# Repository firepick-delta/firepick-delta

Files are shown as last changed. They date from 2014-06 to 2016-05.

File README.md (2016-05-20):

### FirePick Delta Hardware/Mechanical Repo

#### Summary / Context

Design and Manufacturing Specifications for [FirePick Delta](http://delta.firepick.org).  If you're a developer wanting to help, the best way to do that is to join the [mailing list](https://groups.google.com/forum/#!forum/firepick) and start a line of communication there.  

This repo only contains the hardware (sch/pcb) and mechanical (3d) files for FirePick Delta.  It inherits software from OpenPnP, Marlin, and FirePick.  Other repo's of interest for FirePick Delta:

* https://github.com/firepick-delta/openpnp
* https://github.com/firepick-delta/Marlin
* https://github.com/firepick1/FireREST
* https://github.com/firepick1/FireBOM

#### Mechanical Assembly Parts Tree, Instructions, and BOM

Please click the link below to navigate the mechanical assembly with our FireBOM wiki documentation system:

[AFPD0001](AFPD0001) FirePick Delta Hacker-Developer Edition

#### Licensing

CC-BY-SA

These files are licensed under [*Creative Commons Attribution-ShareAlike (CC BY-SA)*](https://creativecommons.org/licenses/by-sa/4.0/legalcode).  Commercial use is OK, but you are required under the license conditions to share your changes with the internet, and also credit the FirePick Delta team.

This license lets others remix, tweak, and build upon your work even for commercial purposes, as long as they credit you and license their new creations under the identical terms. This license is often compared to “copyleft” free and open source software licenses. All new works based on yours will carry the same license, so any derivatives will also allow commercial use. This is the license used by Wikipedia, and is recommended for materials that would benefit from incorporating content from Wikipedia and similarly licensed projects. 

[View License Deed](http://creativecommons.org/licenses/by-sa/4.0/) | [View Legal Code](https://creativecommons.org/licenses/by-sa/4.0/legalcode)

#### Contributors
* [@FlyingLotus1983 (Neil Jansen)](https://github.com/FlyingLotus1983)
* [@firepick1 (Karl Lew)](https://github.com/firepick1)
* [@ChristianLerche (Christian Lerche)](https://github.com/ChristianLerche)
* [@daytonpid (Dayton Pidhirney)](https://github.com/daytonpid)
* [@codedetail (Dave Shanklin)](https://github.com/codedetail)
* [@obnauticus (Thomas Kilbride)](https://github.com/obnauticus)
* [@mstegen (Mike Stegen)](https://github.com/mstegen)
* [@mikeanton (Mike Anton)](https://github.com/mikeanton)

#### Maintainers
* [@FlyingLotus1983 (Neil Jansen)](https://github.com/FlyingLotus1983)
* [@firepick1 (Karl Lew)](https://github.com/firepick1)

#### Contributions and Pull Requests

If you'd like to contribute anything back to this repo, please do so via [pull requests](https://help.github.com/articles/using-pull-requests).  

Keep in mind that the Cubify Design files are binary blobs.  Assembly (AD_ASM) files contain filepath links back to dependent solid parts (AD_PRT), and parts contain filepath links back to the assembly.  This makes it extremely tricky to use version control.  You can't just rename files all willy-nilly, or else Cubify will get very angry.  Please excercise caution and contact the FirePick Delta Dev Team via [google group mailing list](https://groups.google.com/forum/#!forum/firepick) before attempting to modify anything of significant nature.

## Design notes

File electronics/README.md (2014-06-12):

### Electronic Design Directory

To add a new circuit design, first choose a new ID:

* **E** is the ID prefix for electronic parts (e.g., [ECAM01](../../../wiki/ECAM01)).

Archive your new design in git:

1. `git checkout dev`
1. Create a new directory (e.g., **ecam01**) and add your design files
1. `git add --all`
1. `git commit -am "adding new PCB"`
1. `git fetch; git merge; git push`

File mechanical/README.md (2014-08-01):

### 3-D Mechanical Design Directory

#### Summary / Context

This directory contains the mechanical files for  [FirePick Delta](http://delta.firepick.org).  If you're a developer wanting to help, the best way to do that is to join the [mailing list](https://groups.google.com/forum/#!forum/firepick) and start a line of communication there.  

#### Licensing

CC-BY-SA

These files are licensed under [*Creative Commons Attribution-ShareAlike (CC BY-SA)*](https://creativecommons.org/licenses/by-sa/4.0/legalcode).  Commercial use is OK, but you are required under the license conditions to share your changes with the internet, and also credit the FirePick Delta team.

This license lets others remix, tweak, and build upon your work even for commercial purposes, as long as they credit you and license their new creations under the identical terms. This license is often compared to “copyleft” free and open source software licenses. All new works based on yours will carry the same license, so any derivatives will also allow commercial use. This is the license used by Wikipedia, and is recommended for materials that would benefit from incorporating content from Wikipedia and similarly licensed projects. 

[View License Deed](http://creativecommons.org/licenses/by-sa/4.0/) | [View Legal Code](https://creativecommons.org/licenses/by-sa/4.0/legalcode)

#### File Format
These files were created in [Cubify Design](http://cubify.com/Products/Design).  Cubify Design is admittedly not an open-source program, and costs $199 to buy, with a 30-day free trial.  It gives about 50% of the functinoality of SolidWorks, for a fraction fo the price.

We would have loved to use an open-source program for FirePick Delta, but none of them were up to the job.  OpenSCAD, for example, still doesn't (easily) support fillets or other simple primatives.  HOWEVER, we are making the STL versions of these files available now, and will be offering converted versions of all of the mechanical files in this repo in other, more common 3d formats, in the near future, including STEP, IGES, SCAD, and others.  The basic idea is to design in Cubify and, when the files have stabilized, re-draw in industry-standard formats.  

If you're decent with mechanical design software, and would like to volunteer to help us with this effort, please get in touch with us at our [google group malining list](https://groups.google.com/forum/#!forum/firepick).

#### Contributions and Pull Requests

If you'd like to contribute anything back to this repo, please do so via [pull requests](https://help.github.com/articles/using-pull-requests).  

Keep in mind that the Cubify Design files are binary blobs.  Assembly (AD_ASM) files contain filepath links back to dependent solid parts (AD_PRT), and parts contain filepath links back to the assembly.  This makes it extremely tricky to use version control.  You can't just rename files all willy-nilly, or else Cubify will get very angry.  Please excercise caution and contact the FirePick Delta Dev Team via [google group mailing list](https://groups.google.com/forum/#!forum/firepick) before attempting to modify anything of significant nature.

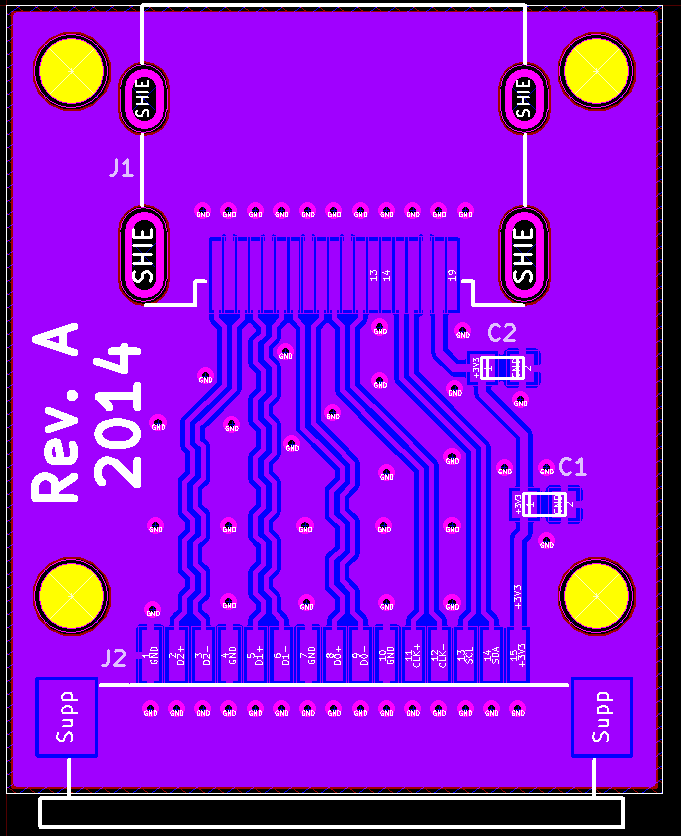
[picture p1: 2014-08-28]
electronics/ehdmifpc01/HDMI to FPC PCB.png

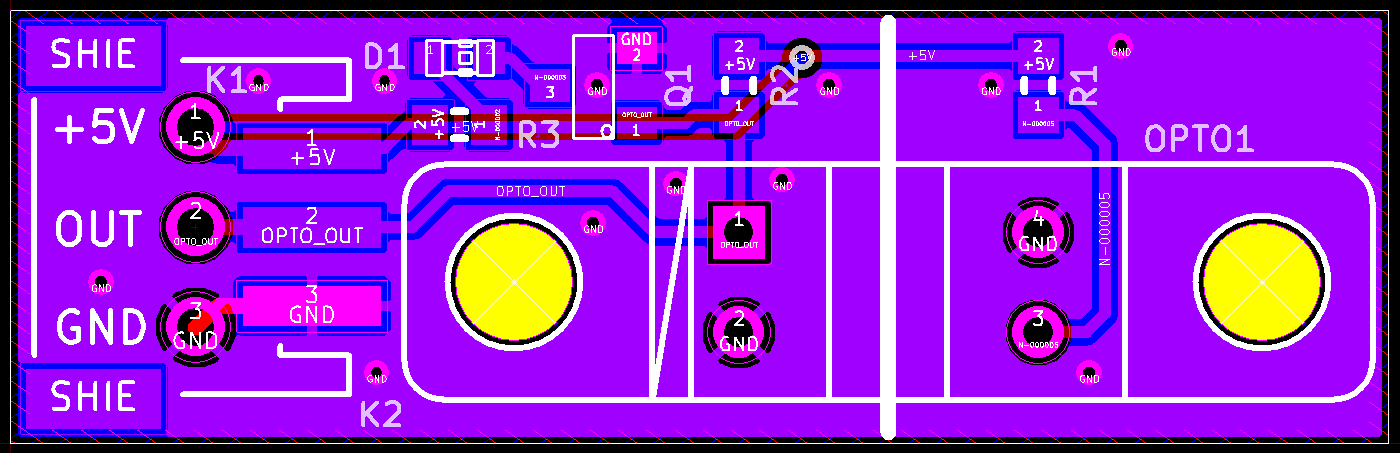
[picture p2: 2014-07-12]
electronics/eopto01/KiCAD/eopto01.png

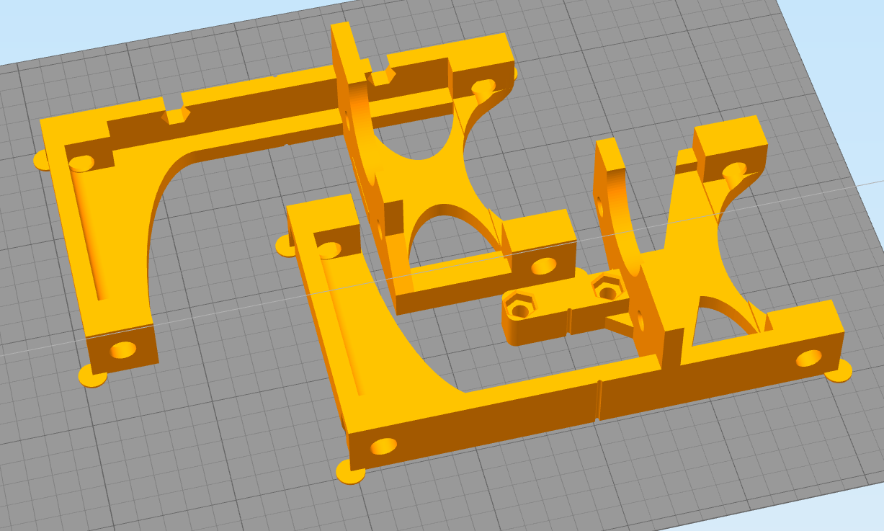
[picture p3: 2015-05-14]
Documentation/STL images/3D0456 Delta stepper mount.png

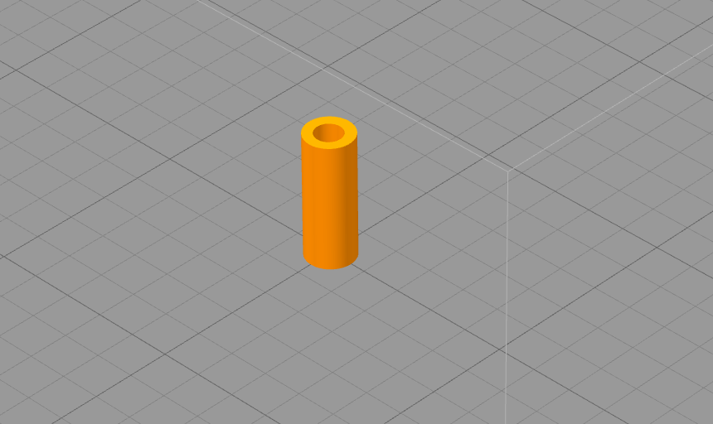
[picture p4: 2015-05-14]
Documentation/STL images/FSTN-M3-18L-UNTHREADED.png

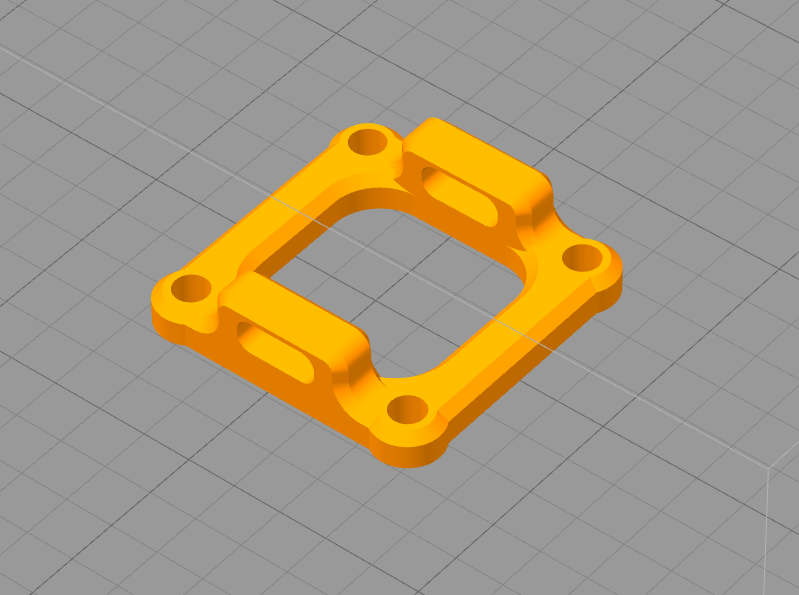
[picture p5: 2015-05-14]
Documentation/STL images/3DAT0015c - Camera-to-end-effector mount - downward endocam.png

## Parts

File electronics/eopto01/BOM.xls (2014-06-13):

Part | Quantity | Price (USD) | Total
--------------------------------------------------------------------------------------------
TCST2103 | 1 | 2.18 | 2.18
Red 0805 LED | 1 | 0.04 | 0.4
10K Resistor 0805 | 1 | 0.04 | 0.04
150 Ohm Resistor 0805 | 1 | 0.04 | 0.04
68 Ohm Resistor 0805 | 1 | 0.04 | 0.04
3 Pin Header “0.1 Spacing | 1 | 0.1 | 0.1
 |  |  | 2.8

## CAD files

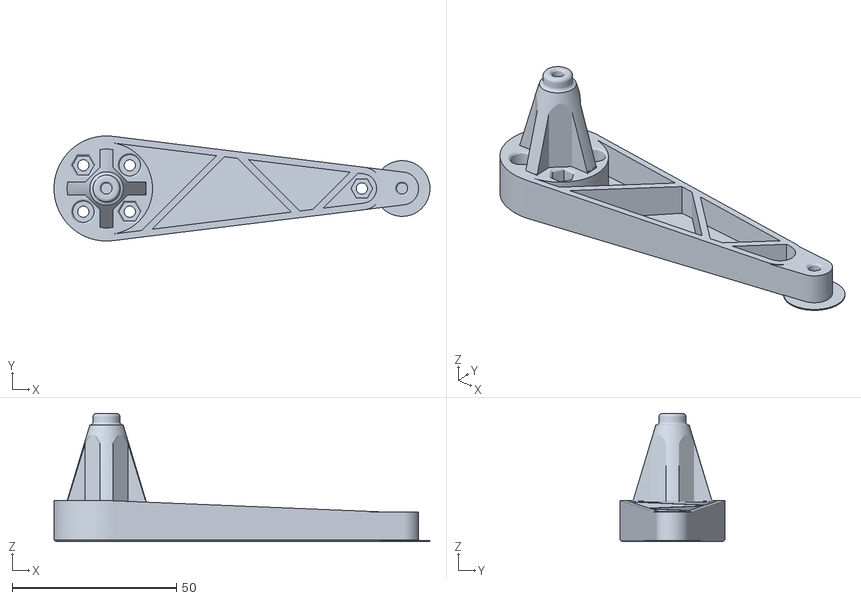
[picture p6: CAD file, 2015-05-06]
Production Files/3D printed pieces - STL - Orange/3D0003a - Delta motor assembly - Delta arm 90mm.stl
114.5 x 32.0 x 39.0

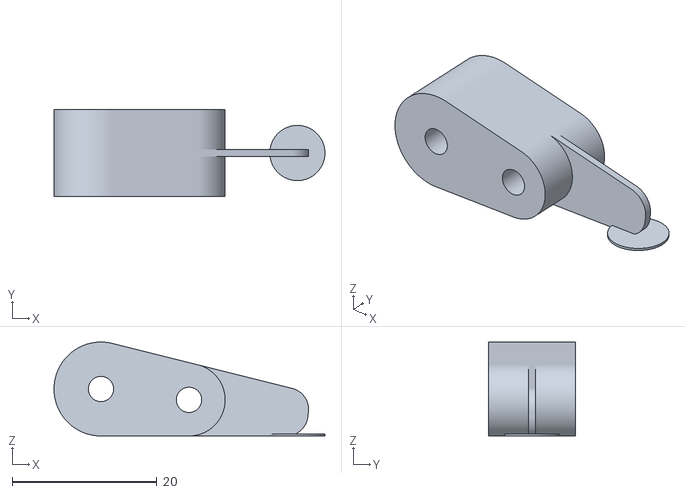
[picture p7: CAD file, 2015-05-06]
Production Files/3D printed pieces - STL - Black/3D0007 - Delta motor assembly - Limit switch interruptor.stl
37.5 x 12.0 x 13.0

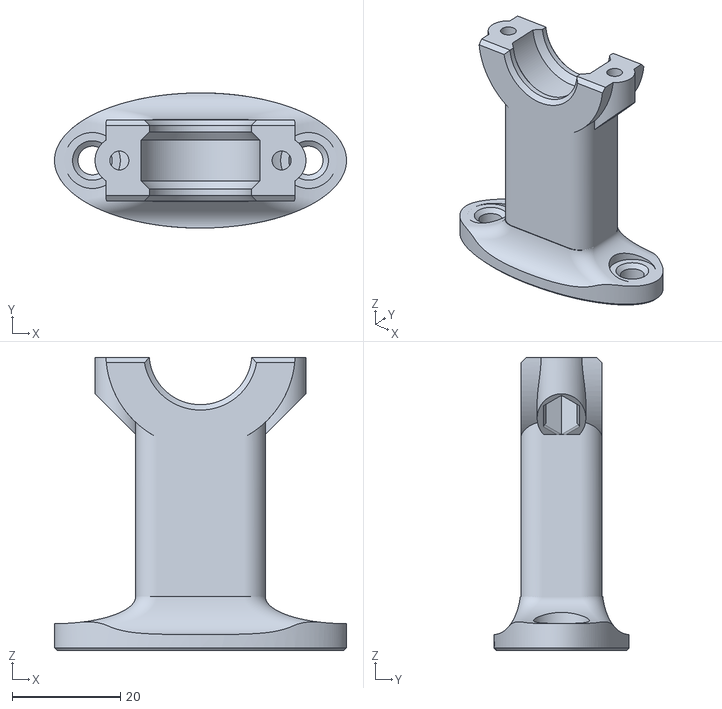
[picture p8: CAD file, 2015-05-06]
Production Files/3D printed pieces - STL - Black/3D0001a - Delta motor Assembly - 608 bearing block.stl
54.0 x 25.0 x 54.3

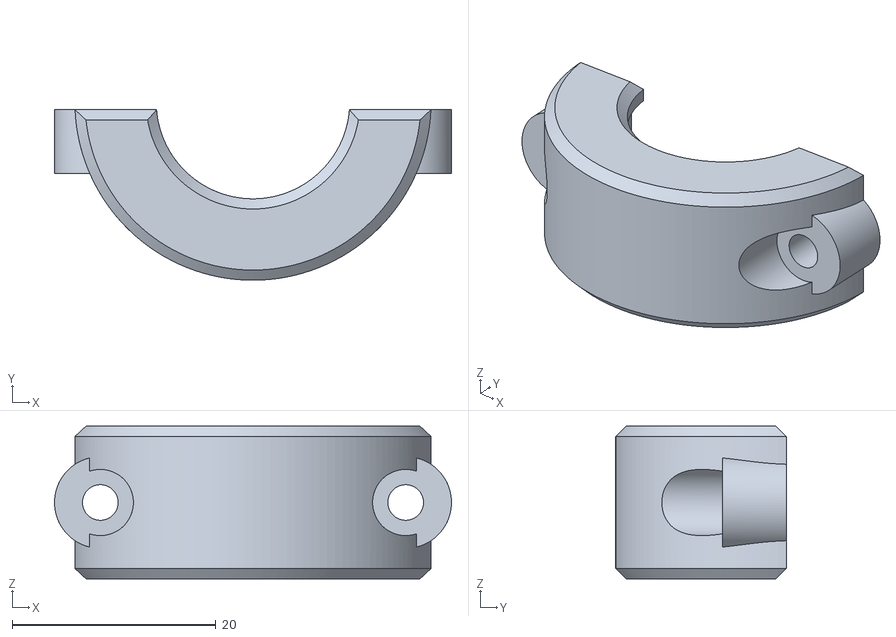
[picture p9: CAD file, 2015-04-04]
Production Files/3D printed pieces - STL - Black/3D0004 - Delta motor Assembly - 608 bearing block caps.stl
39.0 x 16.8 x 15.0

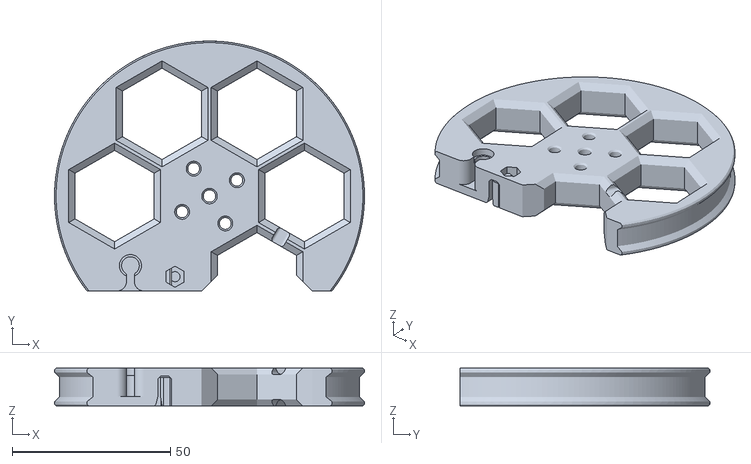
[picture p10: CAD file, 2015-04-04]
Production Files/3D printed pieces - STL - Black/3D0002b - Delta motor assembly - Pulley (150T).stl
98.0 x 79.0 x 12.0

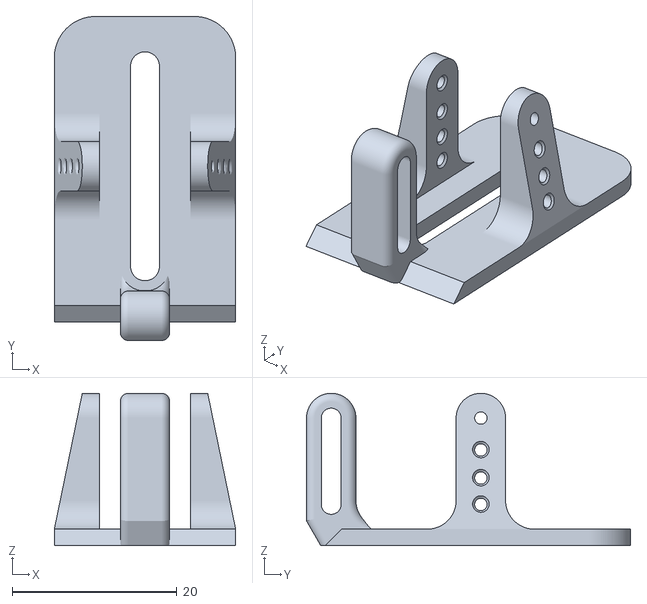
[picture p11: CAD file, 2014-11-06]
mechanical/Hxxx - Hacks/STL/H0003 - Hinged Camera Slide.stl
22.0 x 39.3 x 18.5

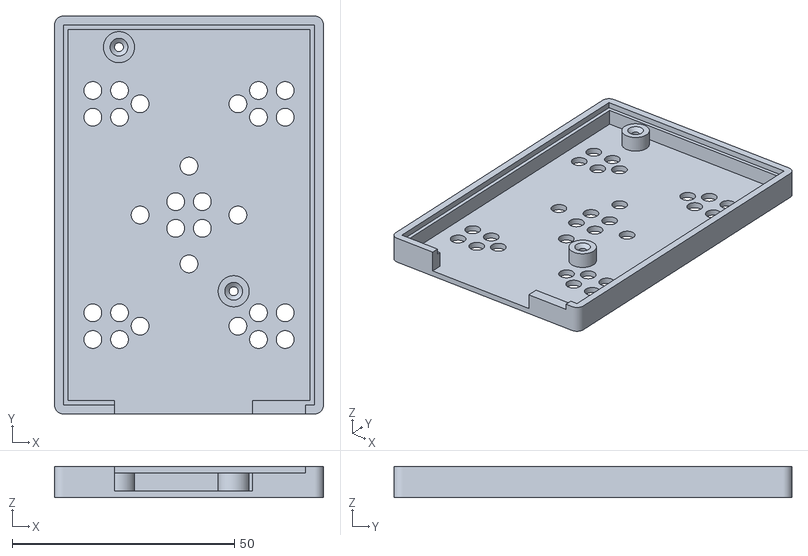
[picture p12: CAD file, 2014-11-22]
mechanical/Jxxx - Jigs and test fixtures/STL/J0013 - RasPi B base.stl
60.5 x 89.5 x 7.00

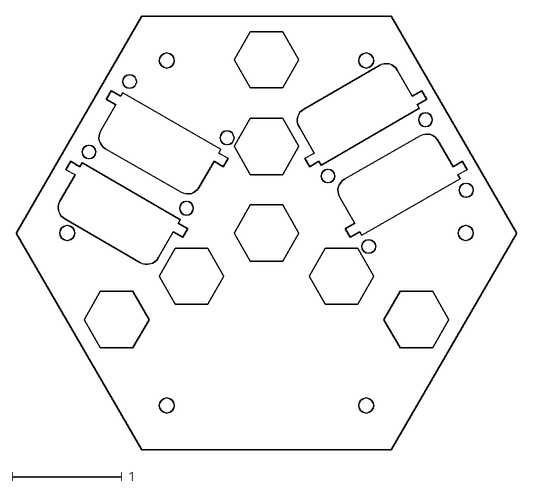
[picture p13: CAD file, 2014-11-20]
mechanical/Pxxx - Panels/DXF/PC04.dxf
4.55 x 3.94

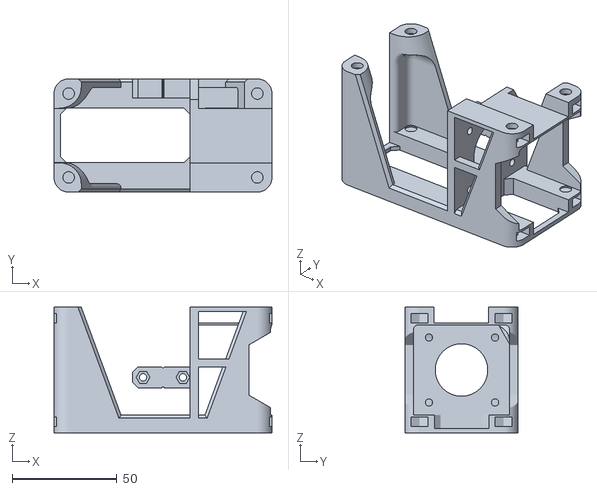
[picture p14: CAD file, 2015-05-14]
Production Files/3D printed pieces - STL - Black/3D0456c Delta stepper mount.stl
104.0 x 54.0 x 60.0

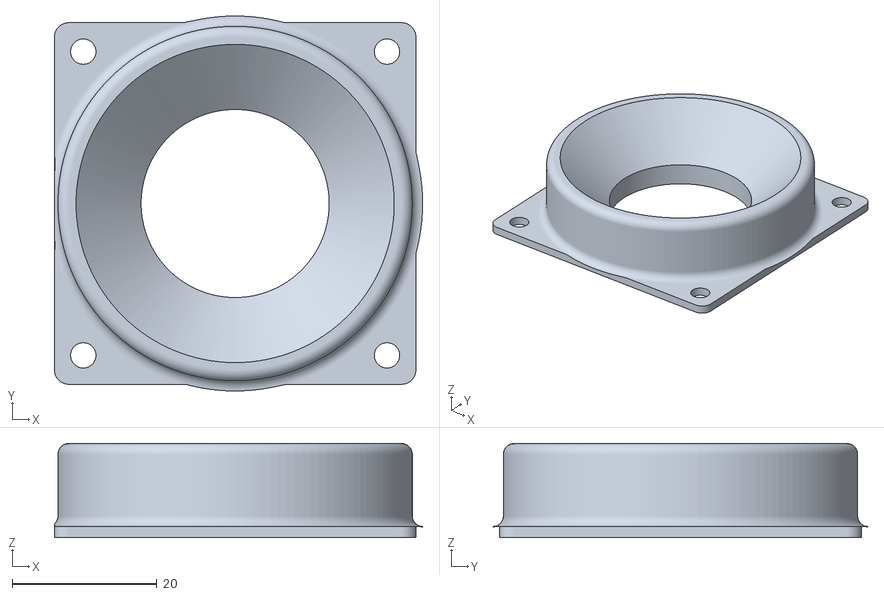
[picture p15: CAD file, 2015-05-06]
Production Files/3D printed pieces - STL - Clear/3D0030b - Up-looking camera housing diffuser - ELP-USB100W03M.stl
50.9 x 51.9 x 13.0

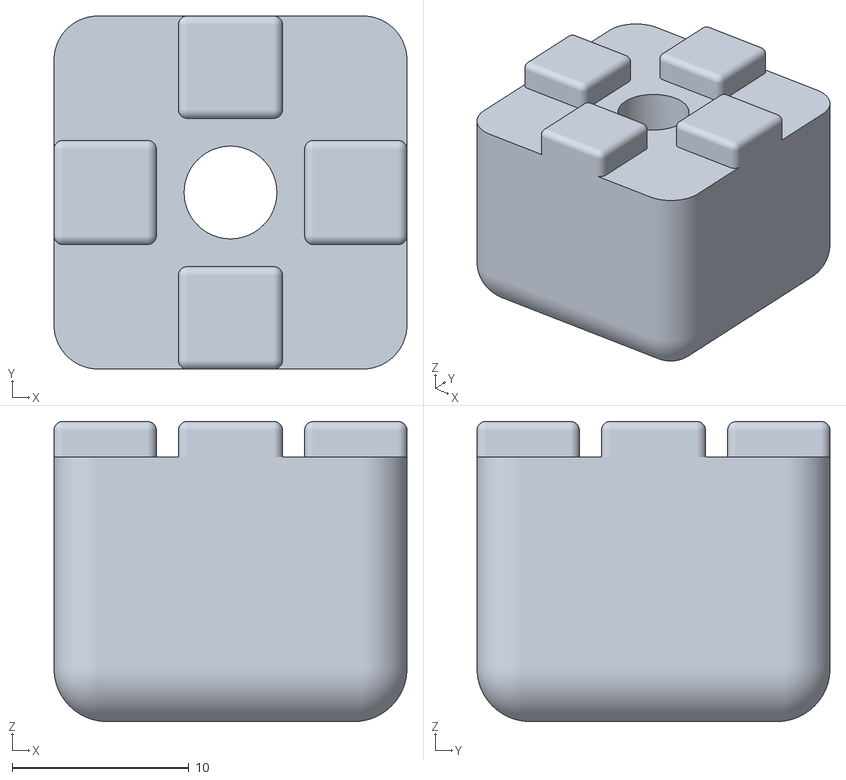
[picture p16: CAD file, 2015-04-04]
Production Files/3D printed pieces - STL - Flexy/3D0025 - Rubber Foot.stl
20.0 x 20.0 x 17.0

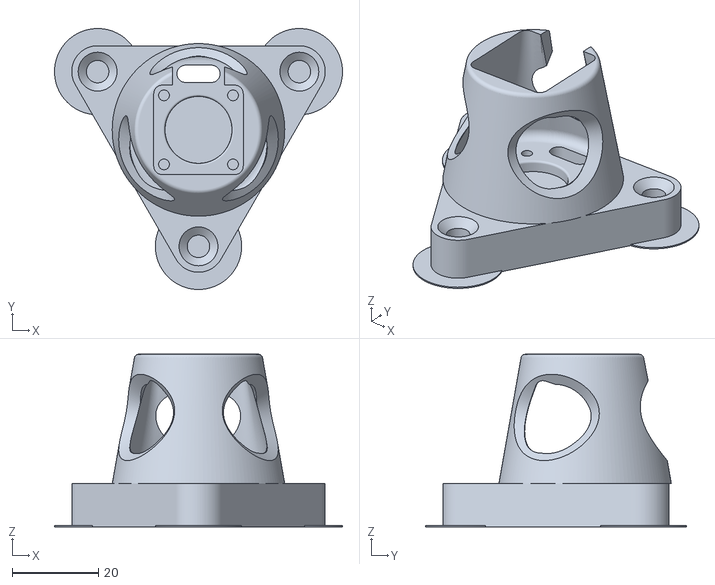
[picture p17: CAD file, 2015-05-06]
Production Files/3D printed pieces - STL - Orange/3DAT0021a - NEMA8 mount.stl
66.8 x 60.5 x 40.0

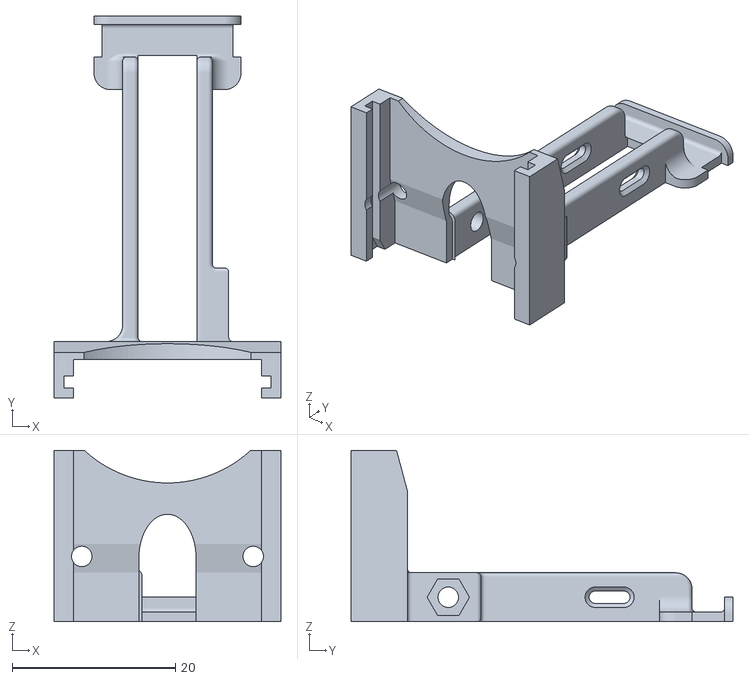
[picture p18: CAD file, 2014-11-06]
mechanical/Hxxx - Hacks/STL/H0002 - RPiCam Hinged Camera Mount.stl
27.8 x 46.7 x 21.0

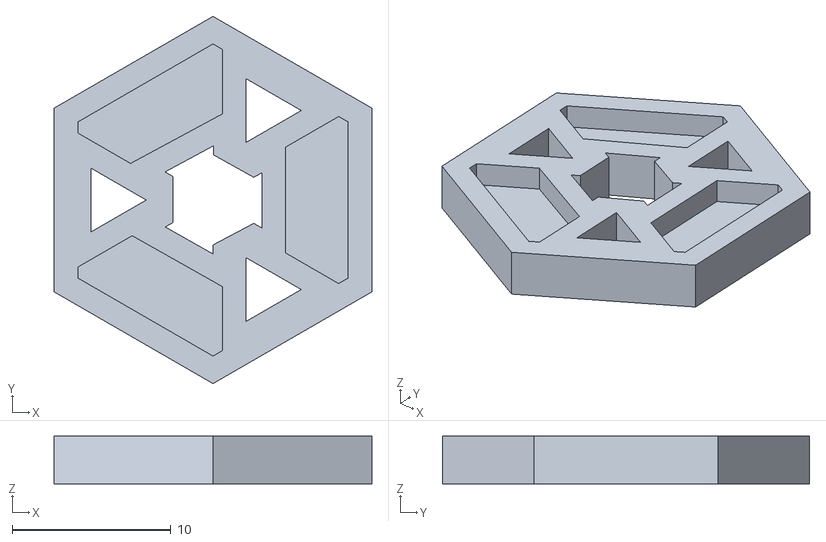
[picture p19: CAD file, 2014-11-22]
mechanical/Jxxx - Jigs and test fixtures/STL/J0001A - Raspberry Pi camera wrench.stl
20.0 x 23.1 x 3.00

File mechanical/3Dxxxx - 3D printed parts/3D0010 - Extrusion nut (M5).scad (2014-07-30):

module box(w,h,d) {
	scale ([w,h,d]) cube(1, true);
}
module hexagon(height, depth) {
	boxWidth=height/1.75;
		union(){
			box(boxWidth, height, depth);
			rotate([0,0,60]) box(boxWidth, height, depth);
			rotate([0,0,-60]) box(boxWidth, height, depth);
		}
}

module nut() {
rotate([180,0,0]) difference() {
	translate([-6, -7.5, 0]) rotate([270,0,0]) linear_extrude(height=15) polygon([ [0,0], [12, 0], [12, 1], [9.2, 3.8], [2.8, 3.8], [0, 1] ]);
	translate([0,0,-1.2]) cylinder(r=5, h=1.2, $fn=100);
	translate([0,0,-4]) rotate([0,0,90]) hexagon(8, 8);
}
}

for(x=[0:6]) for(y=[0:5]) {
	translate([x*13, y*16, 0]) nut();
}

*translate([-6, -7.5, 0]) cube([120, 120, 1]);

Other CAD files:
mechanical/Pxxx - Panels/DXF/PC01 - Top plate.dxf
Production Files/3D printed pieces - STL - Black/3DAT0012a - 3D printer mount_NoSupport.stl
Production Files/3D printed pieces - STL - Clear/3DAT0010a - End effector - ATC hub (bottom).stl
Production Files/3D printed pieces - STL - Orange/3D0053 - External ATX supply coverplate.stl
Production Files/3D printed pieces - STL - Black/3D0010a - Extrusion nut (M3).stl
Production Files/3D printed pieces - STL - Black/3D0015a - EMC02 mounting plate.stl
Production Files/3D printed pieces - STL - Black/3D0021 - EMC01 Modular tool card-cage.stl
Production Files/3D printed pieces - STL - Black/3D0026b - Up-looking camera housing base - ELP-USB100W03M.stl
Production Files/3D printed pieces - STL - Black/3D0028 - PCB magnet holder.stl
Production Files/3D printed pieces - STL - Black/3D0456 Delta stepper mount (unibody).stl
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

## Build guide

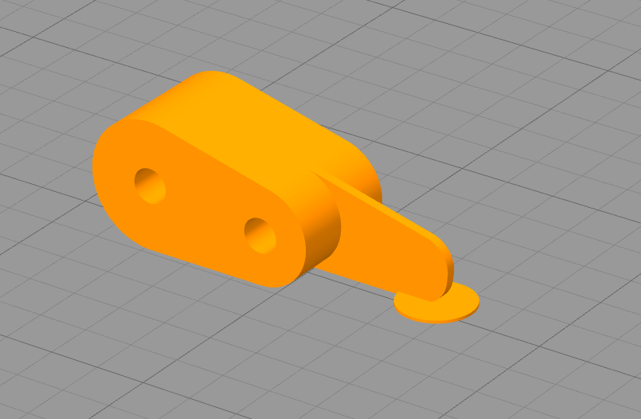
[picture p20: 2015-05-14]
Documentation/STL images/3D0007 - Delta motor assembly - Limit switch interruptor.png

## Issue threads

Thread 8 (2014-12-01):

3D0230a and clearence issues

PeeJay, 2014-12-01:
Hi Neal/Karl
I have just been assembling my arms (the ball end type) and I've had some trouble getting them to fit.
1) The spring (3D0230a) has 2mm holes when both spring socket holders have 3mm - I pressume this is just an oversight, as it all lined up when I printed another set of springs with 3mm holes.
2) When I printed the spring socket holders there was some very slight curling along the edges, but the clearance between the spring and spring socket holders is so small that the upper spring socket holder is binding on the spring. If you look at the lower spring socket holder there is a slit that prevents this binding, so I would suggest to create something similar on the upper spring socket holder.

FlyingLotus1983, 2015-05-30:
Closing issue.  We're not using catenary springs in this repo any more (catenary springs can be found over in Karl's repo, at https://github.com/firepick1/FPD-LooseCanon )

firepick1, 2015-05-30:
For those of you with LooseCanon parts, I apologize for the collision. My interim solution is to use the LooseCanon optical switch interruptor, which has a rake-back angle that prevents the collision. I'll eventually address this, but am currently busy with calibration and motion as a priority.

Closed 2015-05-30.

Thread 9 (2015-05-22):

Outline is in the silkscreen layer, not the dimension issue

FlyingLotus1983, 2015-05-22:
Look through all of the production boards, just to be sure.

bgbock, 2015-05-23:
EPWR01 board

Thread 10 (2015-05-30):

LED ring lights may be too dim -- need weigh-in from the beta test kit owners

FlyingLotus1983, 2015-05-30:

cdsteinkuehler, 2015-05-30:
I think you've got the specs backwards, the white LED has a 3.2V (typ) forward voltage and the red LED has 1.8V.  Given there are two LEDs in series, it seems amazing if the white LED board lights at all (given a combined typical forward voltage of 6.4V)!  The values for the red LED board seem a bit small if you want 10 mA (the value given yields a typical forward current around 13 mA, 150 ohm should yield a bit under 10mA at 5V).  If you want to run the white LEDs off of 5V, they need to each have their own current limiting resistor of around 100 ohms (for 20 mA forward current)...or the existing 120 ohm parts would work well if there weren't two white LEDs in series.

For a short-term fix, I suspect if you simply short across every-other white LED, you'll get much more light output than with the existing circuit.  This should be easy to test, but I don't have the parts to build an LED board, and I didn't get an assembled one in the bare-bones kit.

FlyingLotus1983, 2015-05-30:
Thanks Charles, you're right, I've corrected my initial post with the correct voltages.

If you'd be interested, I could supply you with the red / white LEDs and the 2x BSS138's if you'd be willing to help us with this issue.  I'll mail you the parts free of charge (we have enough of them on a reel, lol).  As for resistors, I recommend this guy: https://www.adafruit.com/products/441 Great tool for any hardware guy's arsenal.

cdsteinkuehler, 2015-05-30:
Send me the LEDs and FETs, the resistor's I've already got on-hand
(all 5% and 1% values between 1R and 10M in 0603 and 0805).  Sometimes
it's handy to design electronics for a living!  :)

IMHO, the LEDs probably ought to be run off 12V if possible,
particularly the white ones.  It's hard to drive that many white LEDs
with only 5V w/o wasting a lot of power (unless you're using "smart"
switching drive circuits to regulate the current instead of plain old
resistors).  Quick back-of-envelope calculation shows if you assume 20
mA LED drive, you're burning 1W in the LEDs, and 600 mW in the
resistors at 5V, or enough you probably need to think about things
getting warm.

--
Charles Steinkuehler
charles@steinkuehler.net

FlyingLotus1983, 2015-05-30:
We're using an ATX power supply for the resistors, sourcing current on the
5V rail won't be a problem.  Putting it on 5V makes the wiring a lot
easier, but I agree that it isn't ideal to drive LEDs with it.

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

--
Neil Jansen, Co-Founder
Tin Whiskers Technology, LLC
http://tinwhiskers.io

rotorfixer, 2015-05-30:
Yes, I have to agree, the source voltage is too low for two of those in series.

Can you post the part numbers of the capacitor and mosfet as well so I can look at supplying the board with 12VDC?

I will also try out Charles' suggestion of using a 0 ohm resistor over one of the LEDs and see what the light output is with half the LEDs, but powered properly.

Peter.

FlyingLotus1983, 2015-05-31:
MOSFET is a standard BSS138 (We used a Fairchild part, digikey P/N is BSS138CT-ND).

Capacitor is a pretty standard electrolytic 16V, 6.3mm diameter, around 100 uF.

Powering the boards with 12V is possible, but the wiring gets a little uglier.

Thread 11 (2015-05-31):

Vacuum pump mount screw is too long

shmuelzon, 2015-05-31:
The vacuum pump mount comes with a 14mm screw in order to mount it to the frame, however I found that this screw is too long and won't hold the mount firmly to the frame. The 10mm ones work great.

FlyingLotus1983, 2015-05-31:
Yikes, I can't believe I missed that.  I'm fixing it on the 3D model now.  Will try and get the BOM and packing list updated as well.

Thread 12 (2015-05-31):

Fan mounting screws are too short

shmuelzon, 2015-05-31:
The screws provided for mounting the fan are too short. It seems that the fan I got is thicker than what was expected (at least it seems higher relative to the drawing)

FlyingLotus1983, 2015-05-31:
This was a screw-up by our Chinese supplier.  We didn't get the fans that we were supposed to. They listed them as 10mm thick and we got these giant monstrosities.  We didn't measure them until after we got a few complaints.

I'm unsure if I should update my model, as it's probably the last time I'm buying from this supplier again, meaning that the BOM and model are actually correct and the fans that are incorrect.  But for the beta kit customers, I will need to send them updates screws for the bigger fans.

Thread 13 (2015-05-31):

No room to mount EAT0002

shmuelzon, 2015-05-31:
There is not enough room to mount the EAT0002 board at slot 1 after I connected the EAT0004 board at slot 2. Perhaps if I remove the heatsink it will fit. I connected the module cards as described in the [documentaiton](http://delta.firepick.org/documentation). See [photo](https://plus.google.com/photos/+AssafInbal/albums/6153966946821929473/6154602321539083746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).

FlyingLotus1983, 2015-05-31:
This is a confirmed issue, I've had to remove the heatsink on my two FPD machines.  The slot spacing on the EMC02 was designed for the EAT0001 style boards that had integrated DRV8825's on the board.  The EAT0002 came later as a way to mitigate some of the SMT produciton issues we were having.  But using the StepStick driver modules are admittedly bulky and cause issues.

Regretfully the short-term workaround is to just run it without the heatsink. The SMT module will be fine like this, and I haven't had issues with the Wade etruder yet.  Will be very interested to see if others have problems.  I'll leave this issue open for the entire beta run, to get more opinions and user accounts.

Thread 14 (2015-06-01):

Missing M3 screw and nut for the small gear of the extruder

shmuelzon, 2015-06-01:
It seems that the exploded view (and, as a consequence, the BOM and beta kit) of the extruder is missing an M3 screw and nut used to attach the small gear to the stepper motor

FlyingLotus1983, 2015-06-02:
This has been fixed in the model, and I will be starting the process of getting the BOM info to trickle down into the packing lists, bag labels, and drawings.  Will keep this issue open until all of that work has been completed, and everyone that ordered full beta kits receives their replacement parts.

FlyingLotus1983, 2015-06-02:
Everything should be updated now.  Some of the thumbnails of the PDF might be out of date, but the google docs PDF is what should be used for reference, and it's been updated in-place without changing the link.  The BOM has been updated as well.

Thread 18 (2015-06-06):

Hobbed bolt not center to input filament

alanNz, 2015-06-06:
For some reason it was way off on mine, I reduce the spacer 3DAT0028 by 3 - 3.5 mm to get alignment

FlyingLotus1983, 2015-06-06:
I designed the spacer specifically for the RobotDigg hobbed bolt's spacing.  On my machines here, they match up perfectly.

I would like to see some measurements from your hobbed bolt to see if it's simply manufacturing variation from the hobbing process, or if it's something else.  The measurement I'm wondering about is from the bottom of the bolt head to the center of the hobbed area.  Could you measure that?  Also, could you post pics of your setup, both assembled and un-assembled?

And is it possible that there's some support material in the bearing pocket of the extruder housing?  That would cause a mis-alignment.  That area needs to be perfectly smooth, and might take a razor blade or other tool to get it perfect.

alanNz, 2015-06-06:
the bearing in the plastic gear side sits flush, the hex head of the bolt sits flush, the pocket looked pretty clean. the Hobbed bolt measurement is 27mm to the center
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

FlyingLotus1983, 2015-06-06:
I think I see the issue now :(

Your spacer should be 8.5mm.  I'm wondering if this was a failed part that should have been thrown away.  Could you send pictures of both top and bottom side?  If this is in fact the problem, I can mail you out a replacement spacer.

The hobbed distance should be at 30mm by the way, so 27 is probably close enough.

alanNz, 2015-06-06:
I've reduced the size of that spacer until it lined up so it probably was a good print. 3mm difference in center is huge! well to me it is lol

I didn't take a before shot unfortunately, it looked like the hobbed bolt would slip/ jam on the filament as it came thru since its going across the smooth section. I've re created what the 3 mm offset looked like in the attached picture.

From a kit point of view you could pack 10 x 1mmwashers so it can be tweaked to overcome manufacturing defects.
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

FlyingLotus1983, 2015-06-06:
OK, I understand now.  I think your hobbed bolt is the problem then.  Sounds like you've made it work, so that's good.  We'll certainly try to come up with a more fool-proof way to do this in the future.  I personally measured 10-15 of them before I made that spacer.  I felt that was better than 4-7 standard M8 washers, which have a pretty significant tolerance stack-up.

alanNz, 2015-06-06:
yea washer's don't look pro either. If you made a 5.5mm plastic spacer + 2mm spacer + 1mm spacer + .5 spacer etc. or 5.5mm, 6.5mm 7.5mm, 8.5mm  etc. Or turn the hobbed bolt into a hobbed threaded rod then you have your double nut on both ends for infinite adjustment.

alanNz, 2015-06-06:
or you just add the step i did, rub spacer on sand paper until it lines up. And then get you bobbed bolt guy to get there act together and spec to +/- 0.5mm which "should" be easy on these!

FlyingLotus1983, 2015-06-06:
Right.  E3D sells a hobbed bolt with threaded ends on both sides, they did this for the same reason.. it makes it a lot more adjustable.  Sadly their price is probably 10x to 25x the price of the one we used in this kit.

alanNz, 2015-06-06:
I always liked the look of these, used in diferent extruder that I've never actually used so cant coment on how well they actually work http://www.aliexpress.com/item/J35-Free-Shipping-Extruder-MK7-Stainless-Steel-Drive-Gear-Hobbed-Gear-For-Reprap-3D-Printer/32219482655.html

FlyingLotus1983, 2015-06-06:
Several problems with those (direct drive) types.  Lower torque, and heat conducted from the stepper motor into the hobbed disc can cause the filament to go mushy.  Lots of people use them, but I've never been a fan of them. I do really like Wade extruders, but as you've seen, they can be trick to setup.  The good news is that after they're setup, they require little to no maintenance, and have proven to be very reliable.

cyberreefguru, 2015-07-30:
I had to shave my space down to ~5.8mm to get the hobbled bolt to align properly.  YMMV.

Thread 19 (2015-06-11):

Effector warping

ristola, 2015-06-11:
Finally got the 3D printer ready and have been working on configuration as it was printing 95% of full size. Was printing 10mm and 20 mm cubes. Everything was perfect.  Then things started changing. Then I started to see the effector is warping and de-laminating.

Hotend temps were at 180c and bed temps at 60c. With hot end fan in operation.
E hot end should is starting to become egg shaped.

Perhaps this should be printed in ABS?
Attached a couple pictures.

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

FlyingLotus1983, 2015-06-11:
This is very concerning.

We've had two demo machines running (videos were posted from Midwest RepRap fest a while ago, and we were also trying to 3d print at SF Maker Faire).  We've got at least dozens of hours of 3D printing so far and haven't seen this.  I've never seen anything like this, actually.

Is your fan blowing "into" the end effector?  Is it wired to +12V, on FAN1?

To me, it actually looks more like the heat from the heated bed is doing that (rather than the hotend heat radiating out that far).

Are you able to confirm the heated bed temperature with an infrared temp gun?

FlyingLotus1983, 2015-06-11:
Actually, I think I might know what it is.

The beta kits have a different thermistor than what I used at MRRF and SF Maker Faire.

I have not programmed this thermistor table into the firmware yet.

Very likely your bed is not running at the right temperature..  I can't say for certain but either way, I should open an issue for this to keep track of the fact that I need to generate this lookup table.

I would not use the heated bed until this table has been created and loaded into the firmware.

ristola, 2015-06-11:
The Hot end'f fan was mounted to blow air across the J-Head.
The Fan is wired to Fan1.

At your request, using a Fluke 561 IR thermometer.. and a Contact Prob at the same time:

Bed Temperature set @ 60C.
Contact Thermocouple is reading - 51C
IR Temperature reading on same location is 52.1 C

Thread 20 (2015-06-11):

Change ELED01 LED series-parallel order per Greg Smart's email

FlyingLotus1983, 2015-06-11:
This change would go onto Rev C of ELED01.  Change circuit so that LED1 and 2 are in parallel, and these to LEDs are in series with R1. Repeat this for all eight strings.

NOTE: Also thinking about changing the wiring pinout of J1, to match a standard RC servo, which are more tolerant to being plugged in backwards.  +5V pin should be the middle pin... This was a mistake on my part.

mikeanton, 2015-06-11:
Please don't configure the LEDs this way in the final design.  LEDs should never be put in parallel, unless they have series resistors as well.  The voltage drop on the two LEDs will not be the same, so they won't get the same current.  I know that wiring LEDs in parallel using the method you describe  is commonly done, but it is a very bad design practice, and usually results in premature LED failure.

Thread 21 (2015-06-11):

EAT0002: Replace single terminal strip with two terminal blocks: One small (thermistor) and one big (heated bed)

FlyingLotus1983, 2015-06-11:

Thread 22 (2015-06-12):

EMC02: Possibly add DC-DC for +5V to future beta tester versions of this PCB

FlyingLotus1983, 2015-06-12:
For example, this converter here:

http://www.recom-power.com/pdf/Innoline/R-78Exx-0.5.pdf

DouglasPearless, 2015-06-12:
Nice wee package.

I am using a LM317 with a resistor to set the voltage and a cap on the in and out legs.

I notice it gets rather warm (no heat sink)

Cheers
Douglas
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

FlyingLotus1983, 2015-06-12:
I put this issue here just for you, Douglas :+1:

Can't say when it'll get done but now we'll have an open issue so it doesn't get forgotten about.

DouglasPearless, 2015-06-12:
Thanks.

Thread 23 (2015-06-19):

ELED02 - 3-pin connector should be moved to side or made to exit the bottom of the module.

FlyingLotus1983, 2015-06-19:
Currently the connector can get bumped and damaged, and it looks unsightly.  Move the connector.

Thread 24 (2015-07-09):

Minor PCB silkscreen error at the heated bed connection

aShure, 2015-07-09:
In the corrected (sic) image for the beta kit hardware round 1 PCB silkscreen: There are two negative (-) pins and no positive (+)
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

The image can be found here: http://delta.firepick.org/beta-kit-hardware-round-1/

FlyingLotus1983, 2015-07-09:
It's on purpose, the + on the bed should go directly to the power supply
per the Dozuki instructions. The Modular tool PCB simply interrupts the
negative wire, sort of like a light switch in household electrical wiring.

The reasoning behind this was that the power comes directly from the power
supply board rather than through the EMC02 board, which isn't able to
source 10+ amps of current through the PCB traces and and the connector(s).

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

--
Neil Jansen, Co-Founder
Tin Whiskers Technology, LLC
http://tinwhiskers.io

dustinkasel, 2015-07-09:
Given that you're using a FET to switch the heater, you have to provide
some kind of polarity marker. The "-" wire from the heater should connect
to the "+" marked terminal.

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

aShure, 2015-07-09:
> It's on purpose, the + on the bed should go directly to the power supply
per the Dozuki instructions. The Modular tool PCB simply interrupts the
negative wire, sort of like a light switch in household electrical wiring.

I see your point, and I second that it makes sense with the high current flowing to the bed. However,  when you look at the PCB, the two pins do not seem to be electrically connected to the same net:

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

Maybe there's a less ambiguous way to describe the connections, there seems to be a lot of space below the headers :)

FlyingLotus1983, 2015-07-09:
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

Ok.

I'll note in the silkscreen.

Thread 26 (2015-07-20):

Heated bed / ground bounce issues

FlyingLotus1983, 2015-07-20:
Peter Shabino posted this to the FirePick group, copying and pasting it here so that it doesn't get forgotten about.
---------------------------------
Finally got the heaters to work as expected. (missed the #def for 3D printing)

While trying to recreate the bed heater fet damage I notice something odd on the graphs. Whenever either of the heaters would turn on both thermistors would drop ~10-20C and when the heaters turned back off the temp would pop back up the same amount.

Poking around the circuit I am seeing  ~30mV of ground bounce on the bed heater thermisor ground pin vs the main power connector ground pin when the hot end heater turns on. The heat bed also cause shifts but no where near as bad since the power and ground lines for the heater run external to the logic cards and directly back to the power supply. Watching the 5V rail on the power supply it jumps up ~20mV when the heaters turn on (loads the 12V regulators which compensate and raise all the voltages in the power supply a small amount.)

Another thing that may cause issues is each thermistor is basically on it's own LDO regulator and not a common domain with the AREF pin on the arduino. Looking though the code I don't see the analogReference() function called so the default of the power rail is used. So the ADC is comparing the voltage divider generated off a random LDO  with the 5V coming out of the PC's USB port. The downside of this is depending on the PC / USB cable you use your reference voltage can very greatly causing all your analog measurements  to be off.

Not sure what smoothies plan is for analog measurements since it is running off 3.3V. But assuming your using the same total temperature range the affect of the ground bounce will only be worse on the temperature reading. To fix this issue you really need to have a dedicated analog ground on which only the tool regulator, eeprom, and thermistor cap are connected. then run a isolated trace from that pin on each module back to the ground pin on the arduino socket. The goal here is to keep any high power current paths from traversing between the arduino and the sensors.

As for the multiple power regulator issues I think we can calibrate the offsets out using the eeproms. BUT... relying on the USB power voltage from a random PC as your reference is a bad idea. Would recommended adding another 5V LDO reg to the AREF pin of the arduino and update the code to use this pin as the ref voltage instead of USB power.

Looking at the 3.3V support I think it is going to cause you headaches when folks switch over to 3.3V boards. The extra voltage divider without a opamp  greatly affects the slope of the response curve by loading down the 4.7k pull up resistor. This can be calibrated out but since it is a nonlinear curve your looking at a lot of work if it has not been done before.  Attached is a quick graph of the output voltage from the two circuits over a small range (thermistor 80 ohms to 90 ohms) normalized to the 5V output levels. Only way to really fix this is to add a voltage follower op amp between the thermistor divider and the 5V to 3V divider. This could go on either the EMC or the EATs.

If you want to simplify things even more on the next pass switch the I2C bus to 3.3V and swap out the 5V LDO on each tool with 3.3V ones. You still need to add a LDO (3.3V in this case) to the arduino but gets around all the messyness with the voltage dividers, opamps, and jumpers. More or less run the 5V arduino at 3.3V analog voltage ref and I2C bus all the time.

But do have some good news...

Verified the hot end and bed temp matches what is reported using my thermocouple reference +/- a degree or two with the heaters off.
The EPO button does shut down the Heaters when pressed.

So far no issues with the Hot bed fet... BUT I may have wired mine differently than everyone else. On my machine I have a dedicated 16 gauge wire pair from the power supply 12V2 and ground pins up to the EAT. Then from the EAT down to the heater bed I have 18 gauge wire. With this setup I see a IR drop voltage (measured from the  power supply ground pin on the EAT to the power supply ground pin on the EMC) of 0.275V. Across the fet I see a drop of 0.091V and a current draw of 7.7A which gives the power loss in the fet of about 0.75W. They fet on mine stayed cold to the touch even after running the heat bed up to 110C.

Would be interesting to see what kind of voltage drop folks are seeing on a official build between Logic reference ground on the EMC and the power supply ground input pin on the ETA. If this drop was significantly higher It would explain any fet heating / death.

It is very late here now so excuse anything that came across as gibberish. Brain is already starting to fall asleep.

Later,
Peter

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

DouglasPearless, 2015-07-20:
Hi Peter,

As I am using a MotionBoard now, the LDO regulators on my EAT00x boards are all 3v3 LDO parts so my EAT00x boards are 3v3 and not 5v ones.

On my EMC02 I set the jumpers for the AIN pins to 5V to short out the inline resistor that is there so the circuit looks the same as the one Smoothie uses EXCEPT for the power to the Thermistor, it is via the LDO.

I am looking at grabbing one of my ‘spare’ EAT001’s and routing just the 3V3 used by the thermistor via a wire directly to the analog reference on the MotionBoard and this will make the analog circuit identical to Smoothie to see if this works better.

Neil: Are you open to changes to the interface to the tool boards, primarily to bring an AREF to the board?

Cheers
Douglas
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

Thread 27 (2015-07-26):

Symptom: Heated bed fet failure. Possible root cause damaged 74ACT244 buffer.

Wireb, 2015-07-26:
Folks experimenting with 3D printing have been reporting the FET on the EAT controlling the heated bed are failing.

Inital thoughts was the FET was getting put into the linear range instead of either fully on or fully off. Checked my setup for excessive IR drop and improper inputs and no issues were found. Someone on the forums noted the 74ACT244 had failed on their card resulting in the output going to ~3V. This would put the fet in the linear region and cause thermal failure.

Potential root cause for the 74ACT244 failure is the fact that the inputs from the Arduino/Smootie are potentially active when the power rail to the 74ACT244 is off. This is due to the micro being on 5V/3.3V standby while the 74ACT244 is on bulk power. Per the datasheet the inputs absolute maximum is Vcc+0.5V which in this case is exceeded.

Recommendation is to switch t0 a 74AHCT244, http://www.digikey.com/product-detail/en/74ACT244MTCX/74ACT244MTCXTR-ND/965167 is a drop in replacement. The inputs on these are rated to +7V under all conditions. They should be able to handle the case where the micro is on but the bulk power rail to the 74AHCT244 is off.

Currently fix is not verified as I am not set up for 3D printing yet. Other have indicated they are going to try it. Once someone has upgraded the parts and run for a few weeks with no failures I think this can be closed.

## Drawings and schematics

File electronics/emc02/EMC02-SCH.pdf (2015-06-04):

E-STOP | DOUT 3.3V->5V BUFFERING | EN BUFFERING | MODULAR TOOL SYSTEM

A

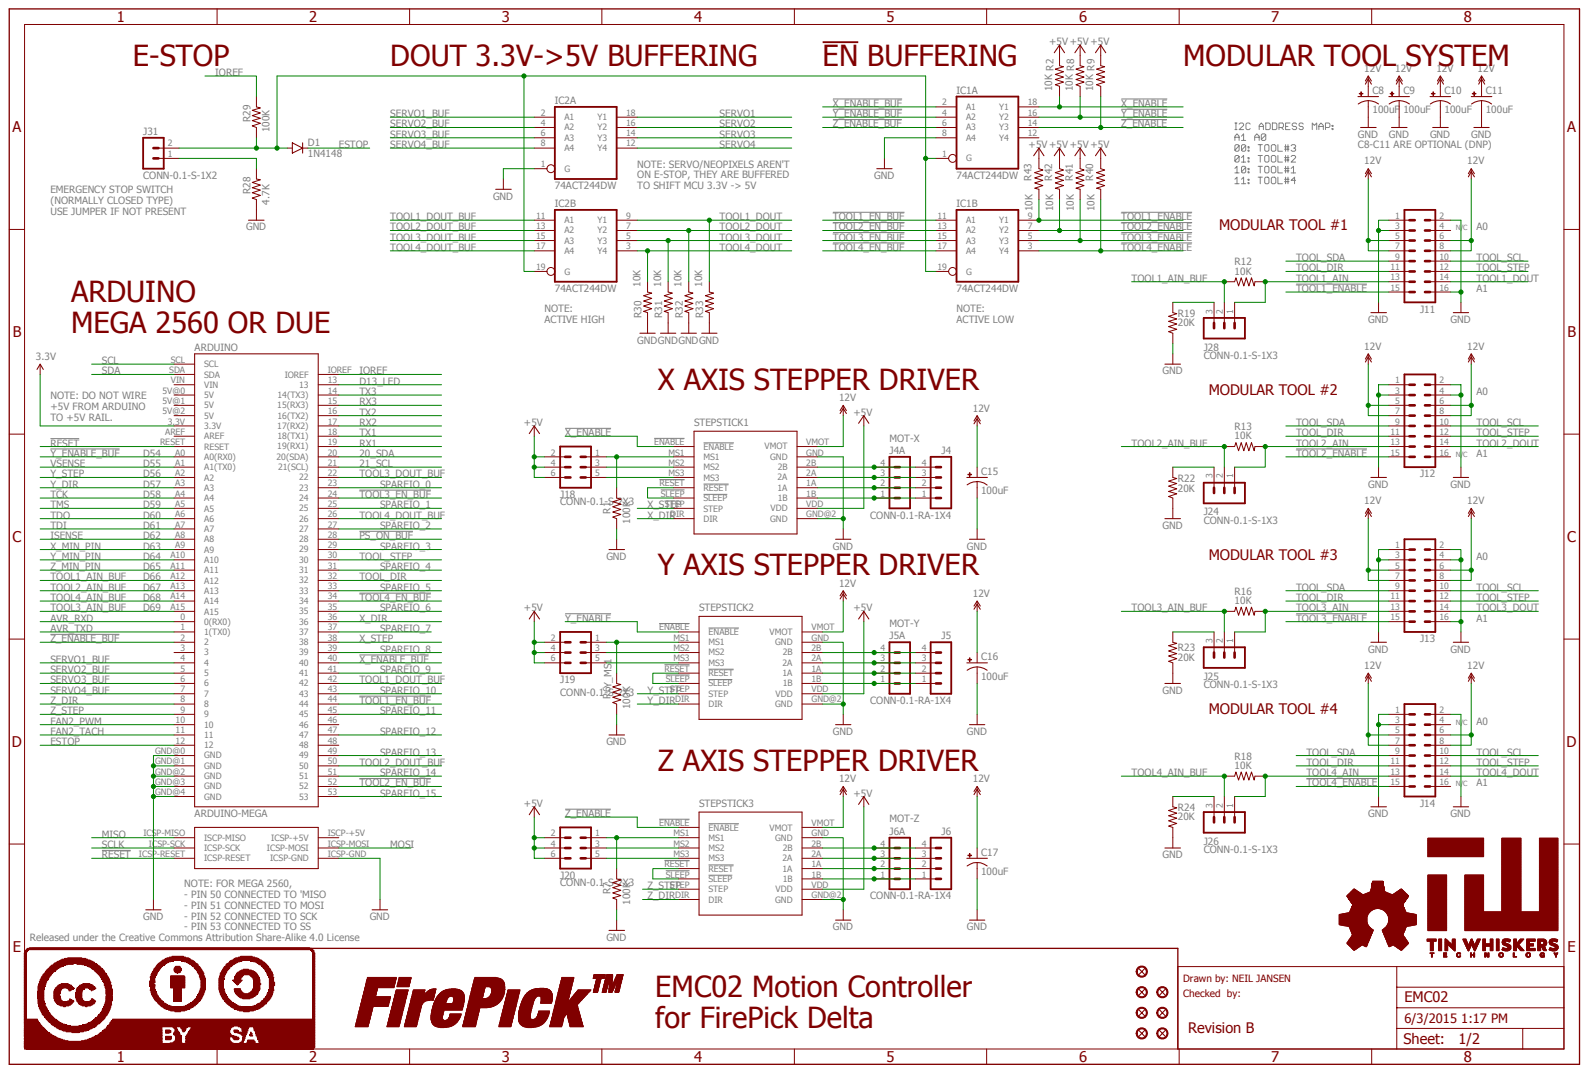
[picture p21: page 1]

IOREF ARDUINO

NOTE: SERVO/NEOPIXELS AREN'T
ON E-STOP, THEY ARE BUFFERED
TO SHIFT MCU 3.3V -> 5V

EMERGENCY STOP SWITCH
(NORMALLY CLOSED TYPE)
USE JUMPER IF NOT PRESENT

NOTE: DO NOT WIRE
+5V FROM ARDUINO
TO +5V RAIL.

ISCP-MISO ICSP-MISO
ICSP-SCK
ICSP-RESET

NOTE: FOR MEGA 2560,
- PIN 50 CONNECTED TO 'MISO
- PIN 51 CONNECTED TO MOSI
- PIN 52 CONNECTED TO SCK
- PIN 53 CONNECTED TO SS

Released under the Creative Commons Attribution Share-Alike 4.0 License

Drawn by: NEIL JANSEN
Checked by:
Revision B

# +12V FANS

SERVOS OR NEOPIXELS | RESET BUTTON | STATUS LEDS

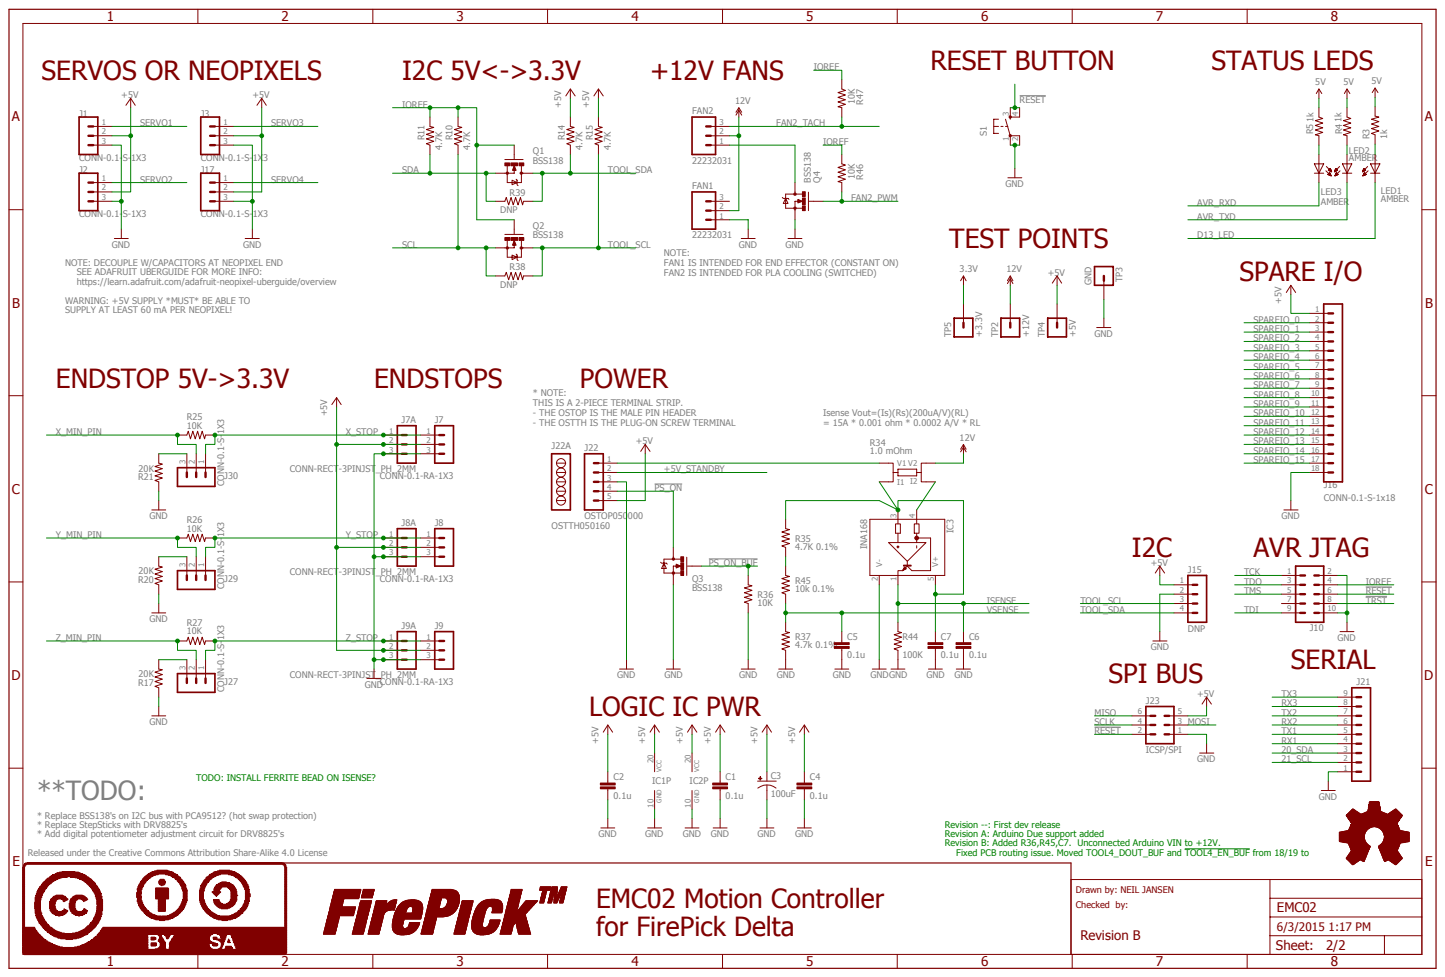
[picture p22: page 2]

NOTE: DECOUPLE W/CAPACITORS AT NEOPIXEL END
SEE ADAFRUIT UBERGUIDE FOR MORE INFO:
https://learn.adafruit.com/adafruit-neopixel-uberguide/overview
WARNING: +5V SUPPLY *MUST* BE ABLE TO
SUPPLY AT LEAST 60 mA PER NEOPIXEL!

* NOTE:
THIS IS A 2-PIECE TERMINAL STRIP.
- THE OSTOP IS THE MALE PIN HEADER
- THE OSTTH IS THE PLUG-ON SCREW TERMINAL

Isense Vout=(Is)(Rs)(200uA/V)(RL)
= 15A * 0.001 ohm * 0.0002 A/V * RL

TODO: INSTALL FERRITE BEAD ON ISENSE?

* Replace BSS138's on I2C bus with PCA9512? (hot swap protection)
* Replace StepSticks with DRV8825's
* Add digital potentiometer adjustment circuit for DRV8825's
Released under the Creative Commons Attribution Share-Alike 4.0 License

Revision --: First dev release
Revision A: Arduino Due support added
Revision B: Added R36,R45,C7. Unconnected Arduino VIN to +12V.
Fixed PCB routing issue. Moved TOOL4_DOUT_BUF and TOOL4_EN_BUF from 18/19 to

Drawn by: NEIL JANSEN
Checked by:
Revision B

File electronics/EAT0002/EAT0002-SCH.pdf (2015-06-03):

# MODULAR TOOL CONNECTOR

A

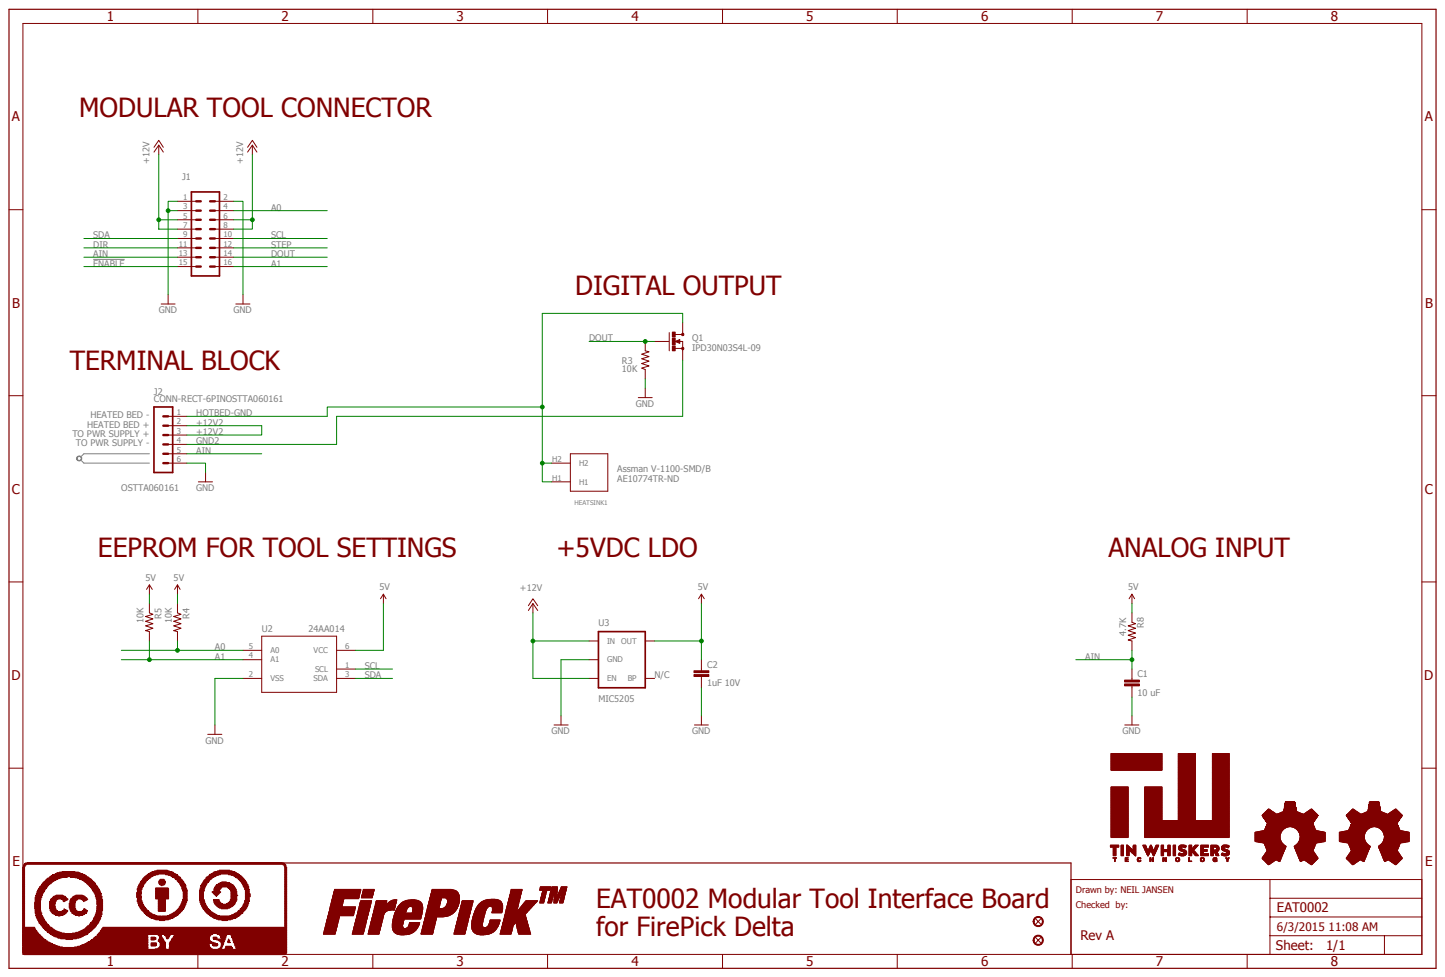
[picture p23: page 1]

EAT0002 Modular Tool Interface Board
for FirePick Delta

Drawn by: NEIL JANSEN
Checked by:
Rev A

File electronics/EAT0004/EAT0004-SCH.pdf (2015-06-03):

# MODULAR TOOL CONNECTOR

A

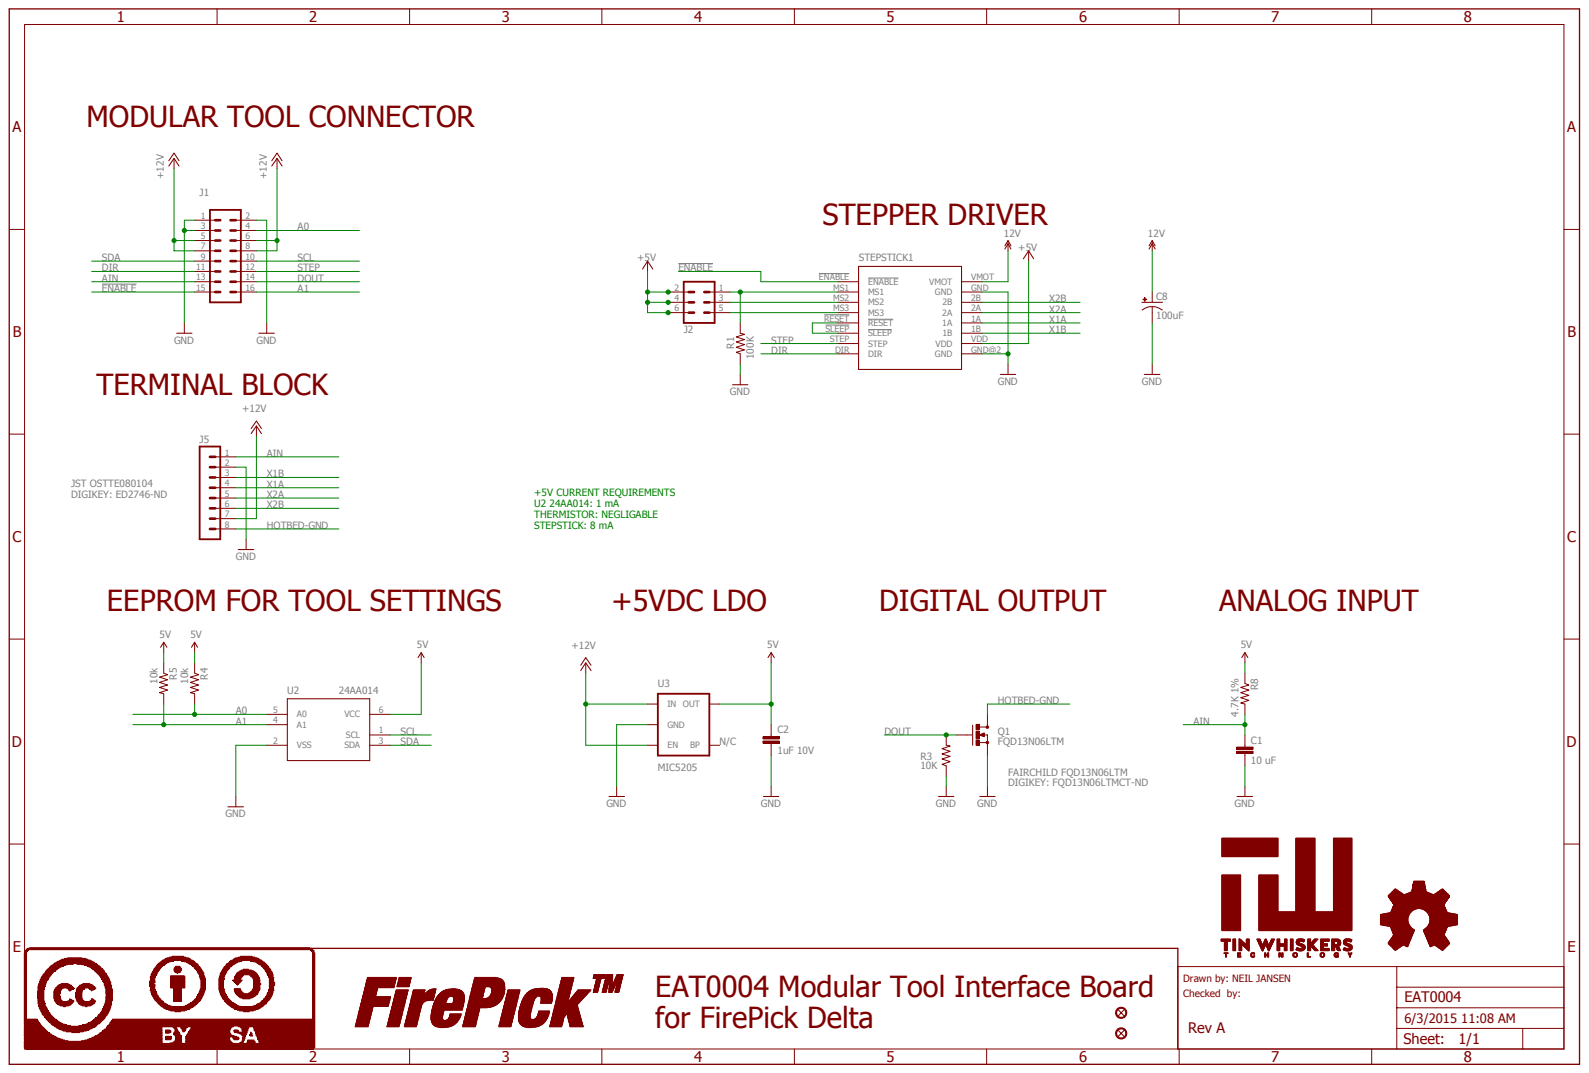
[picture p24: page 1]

EAT0004 Modular Tool Interface Board
for FirePick Delta

Drawn by: NEIL JANSEN
Checked by:
Rev A

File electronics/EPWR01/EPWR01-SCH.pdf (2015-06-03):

A

A

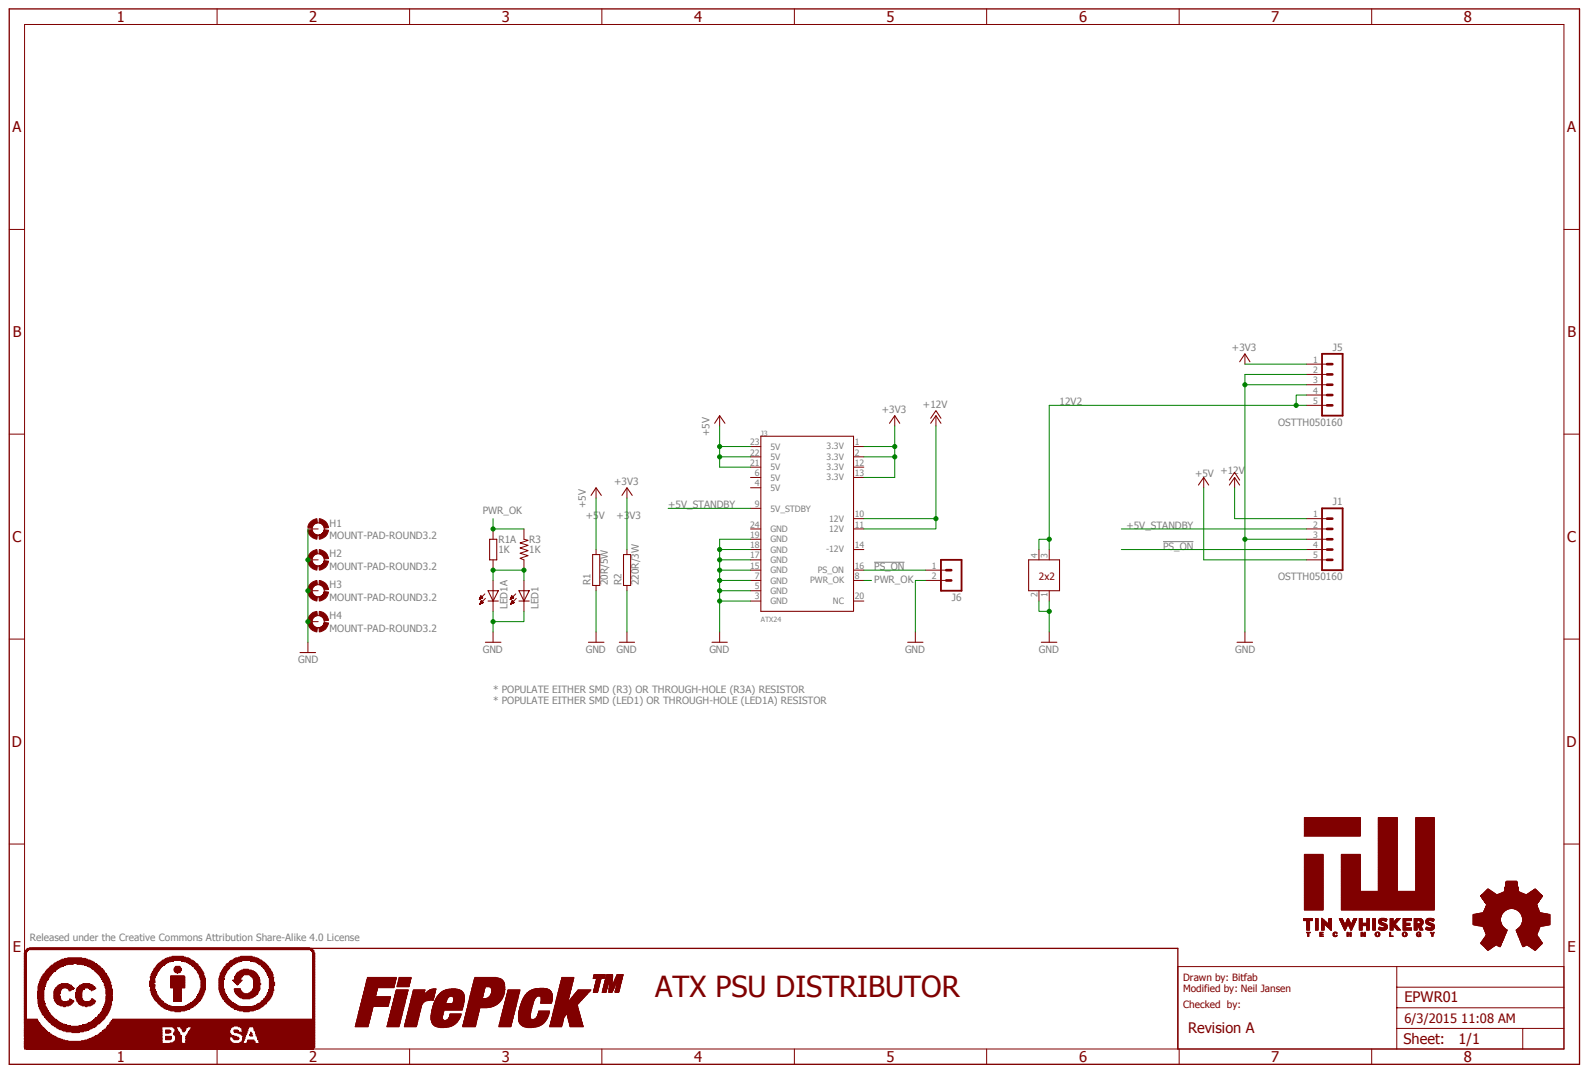
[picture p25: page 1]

* POPULATE EITHER SMD (R3) OR THROUGH-HOLE (R3A) RESISTOR
* POPULATE EITHER SMD (LED1) OR THROUGH-HOLE (LED1A) RESISTOR

Released under the Creative Commons Attribution Share-Alike 4.0 License

Drawn by: Bitfab
Modified by: Neil Jansen
Checked by:
Revision A

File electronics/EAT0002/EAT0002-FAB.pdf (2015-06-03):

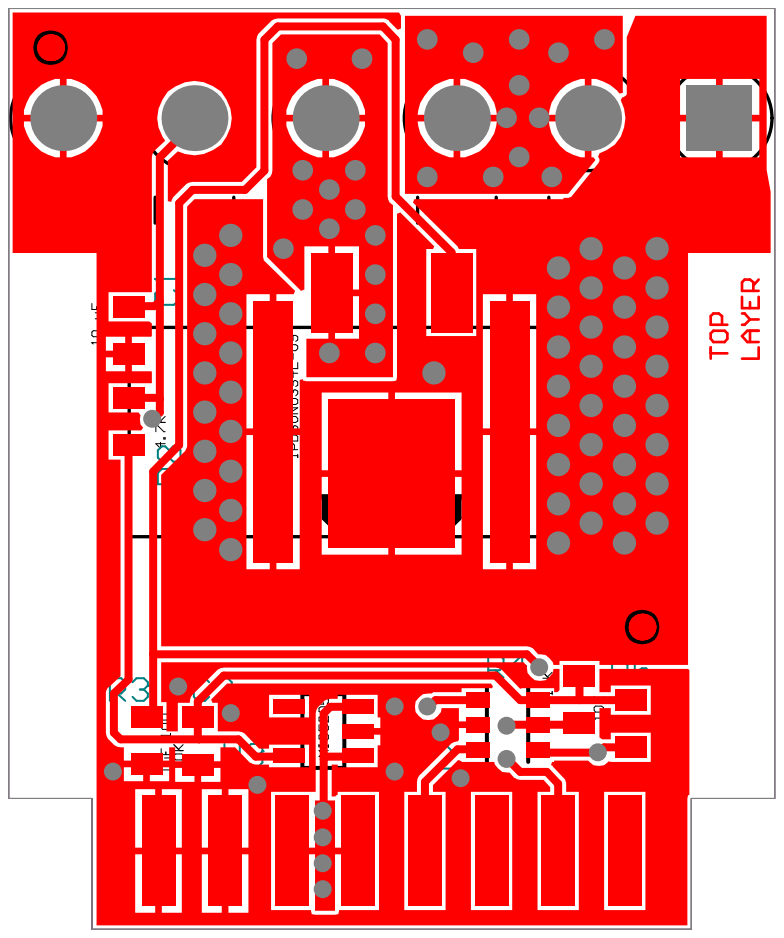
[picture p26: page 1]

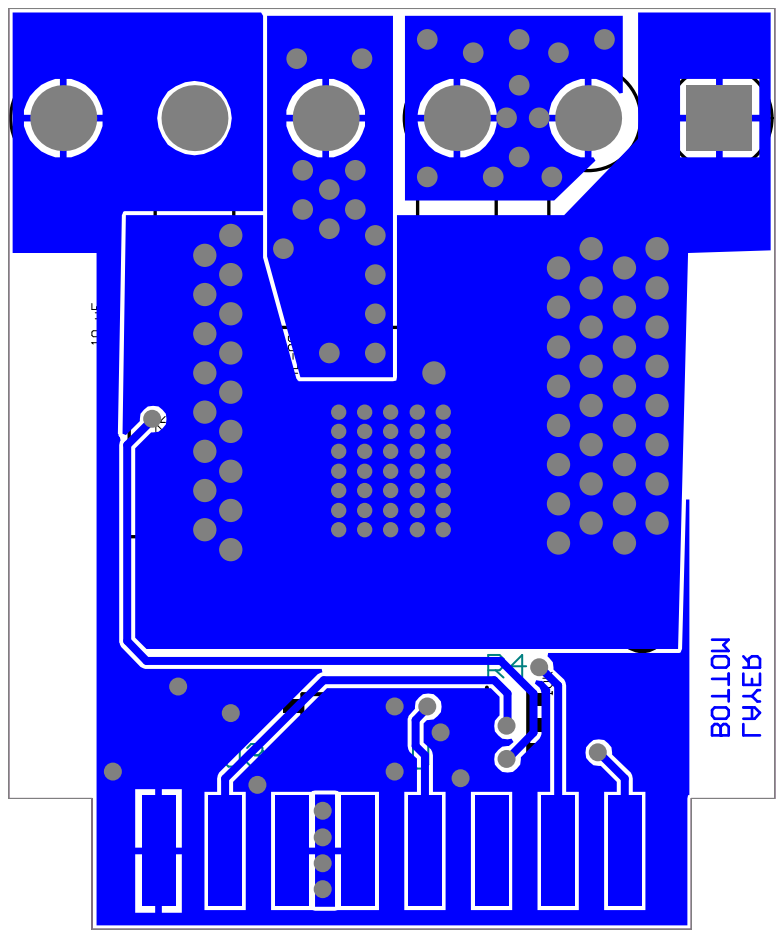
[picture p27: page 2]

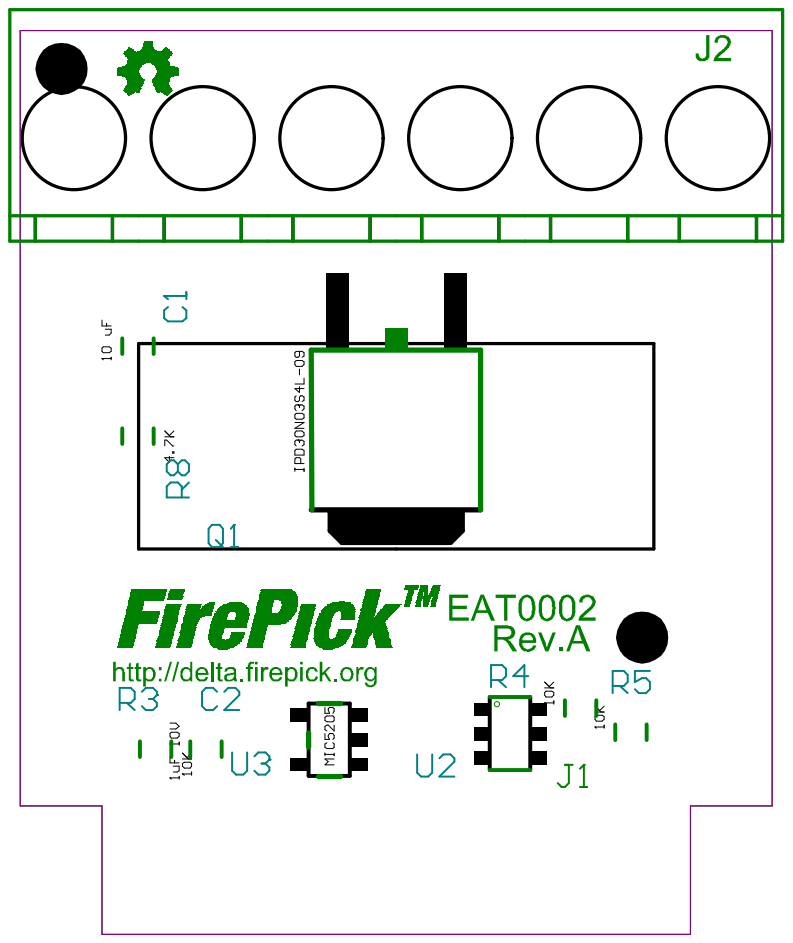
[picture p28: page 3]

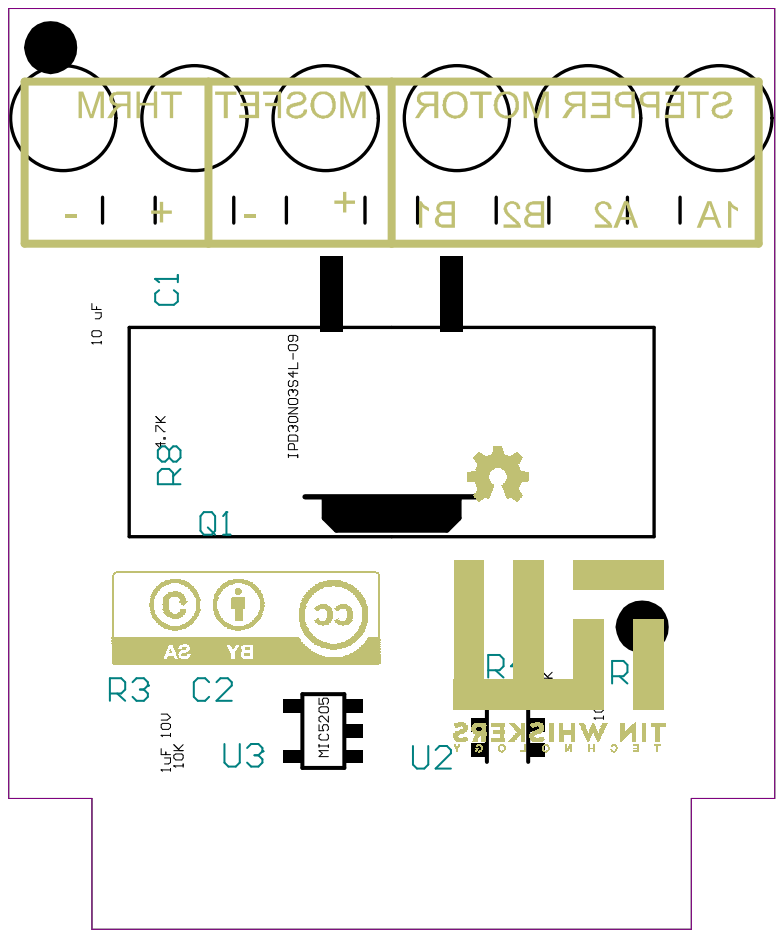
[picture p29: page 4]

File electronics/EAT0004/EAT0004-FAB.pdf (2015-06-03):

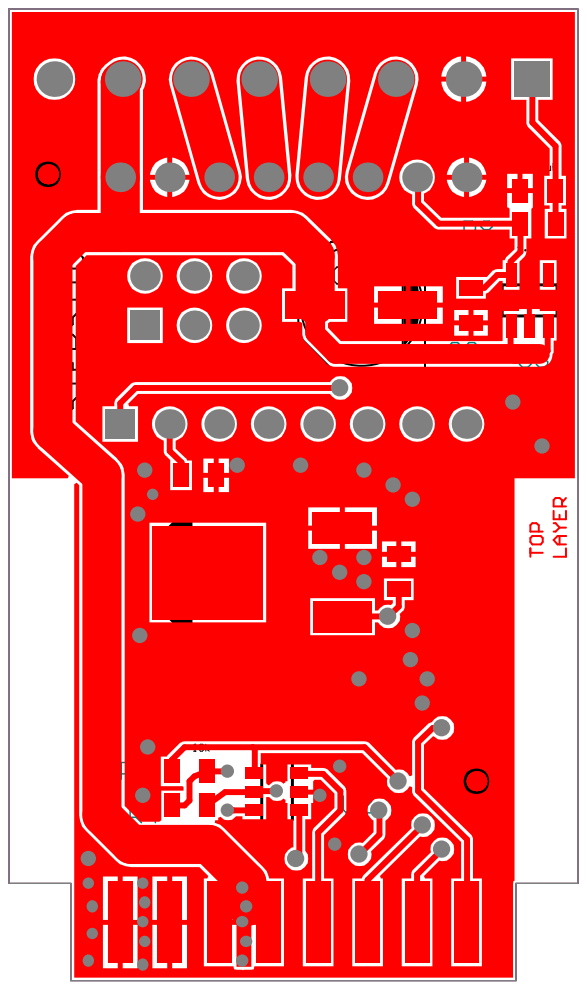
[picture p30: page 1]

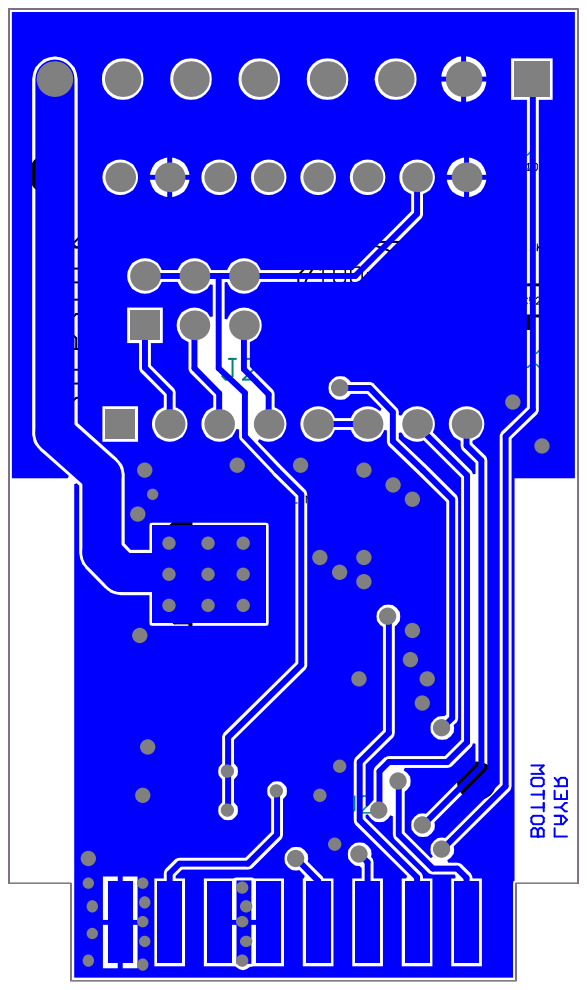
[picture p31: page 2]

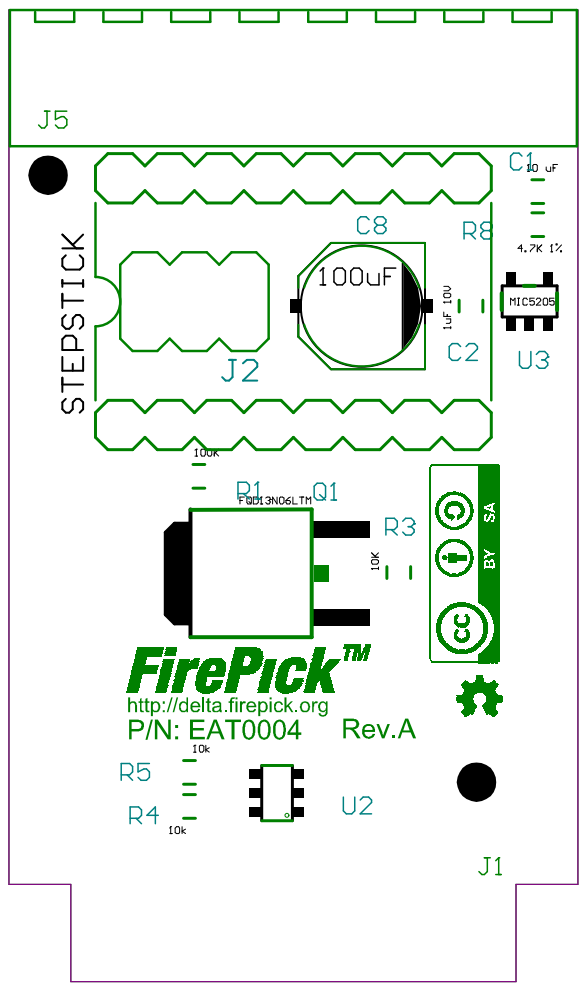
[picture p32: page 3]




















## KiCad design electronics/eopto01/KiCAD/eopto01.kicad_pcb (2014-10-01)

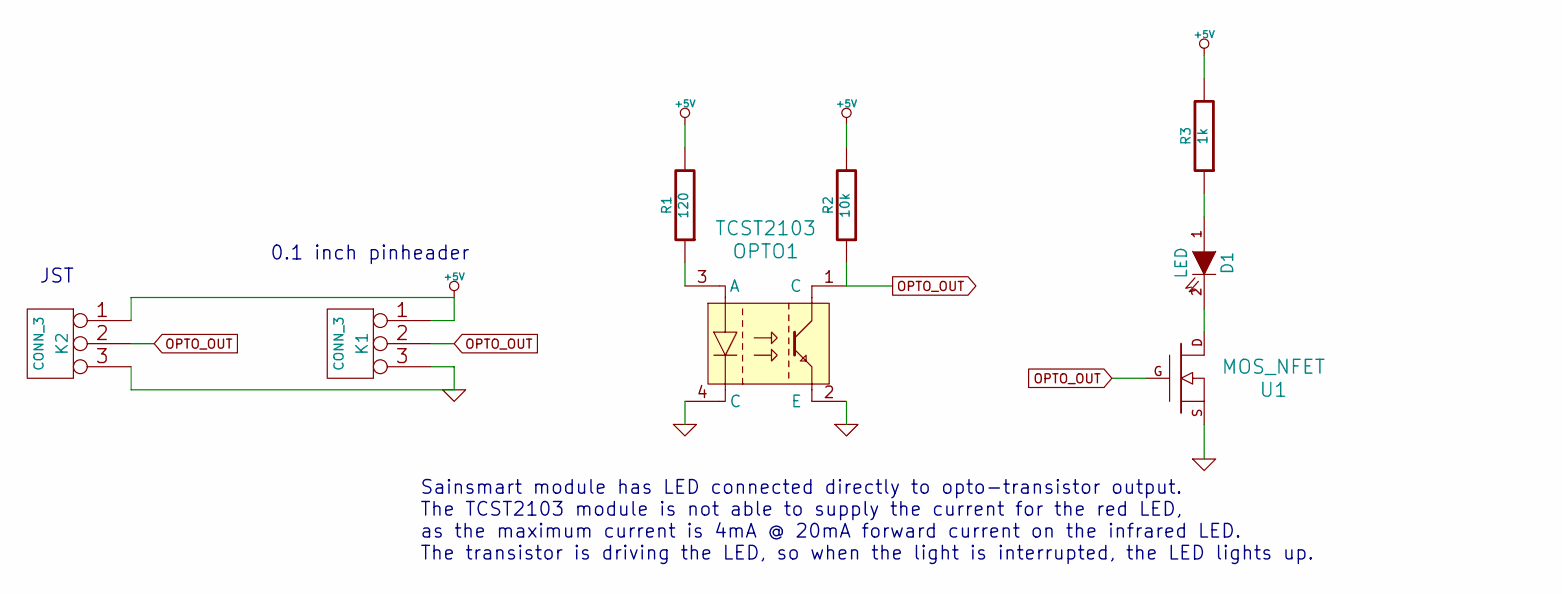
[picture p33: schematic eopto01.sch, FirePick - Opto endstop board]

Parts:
D1: LED
K1, K2: CONN_3
OPTO1: TCST2103
R1: 120
R2: 10k
R3: 1k
U1: MOS_NFET

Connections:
+5V: K1.1, K2.1, R1.2, R2.2, R3.2
GND: K1.3, K2.3, OPTO1.2 (E), OPTO1.4 (C), U1.2 (S)
unnamed: D1.1 (A), R3.1
unnamed: D1.2 (K), U1.3 (D)
unnamed: OPTO1.3 (A), R1.1
OPTO_OUT: K1.2 (PM), K2.2 (PM), OPTO1.1 (C), R2.1, U1.1 (G)

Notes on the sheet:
Sainsmart module has LED connected directly to opto-transistor output. The TCST2103 module is not able to supply the current for the red LED, as the maximum current is 4mA @ 20mA forward current on the infrared LED. The transistor is driving the LED, so when the light is interrupted, the LED lights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
JST
0.1 inch pinheader

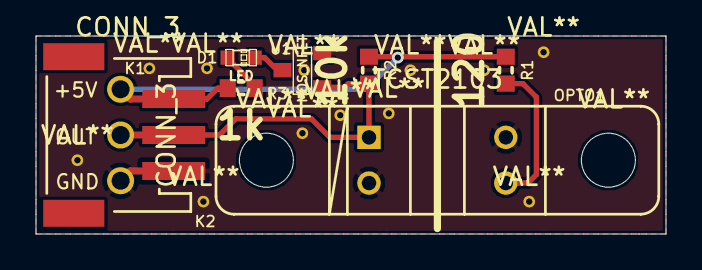
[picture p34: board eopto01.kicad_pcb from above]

Board: 2 copper layers, 35.0 x 11.0 mm, 8 parts (0 on the bottom side), 6 nets.

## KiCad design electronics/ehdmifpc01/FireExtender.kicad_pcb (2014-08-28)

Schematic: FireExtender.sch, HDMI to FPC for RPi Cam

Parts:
C1, C2: 0.1uF
J1: HDMI_TYPE_A
J2: CONN_15_RPI-CAM

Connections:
/+3V3: C1.1, C2.1, J1.18, J2.15
/CLK+: J1.10, J2.11
/CLK-: J1.12, J2.12
/D0+: J1.7, J2.8
/D0-: J1.9, J2.9
/D1+: J1.4, J2.5
/D1-: J1.6, J2.6
/D2+: J1.1, J2.2
/D2-: J1.3, J2.3
/SCL: J1.15, J2.13
/SDA: J1.16, J2.14
GND: C1.2, C2.2, J1.2, J1.5, J1.8, J1.11, J1.17, J2.1, J2.4, J2.7, J2.10

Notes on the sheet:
HDMI to FPC connector for RPi CAM

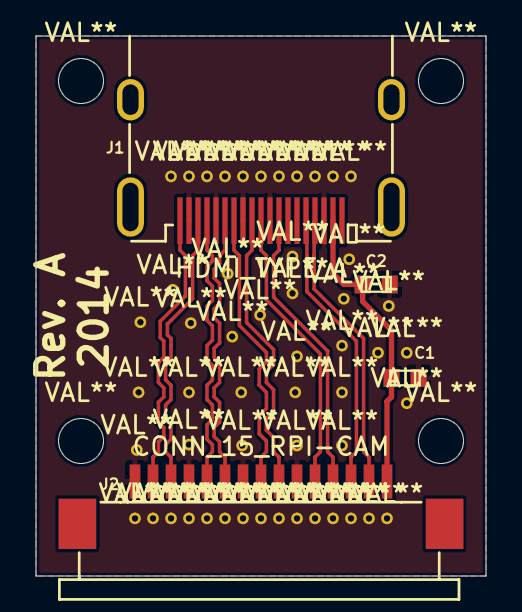
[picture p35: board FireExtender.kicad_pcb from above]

Board: 2 copper layers, 25.0 x 30.0 mm, 4 parts (0 on the bottom side), 12 nets.

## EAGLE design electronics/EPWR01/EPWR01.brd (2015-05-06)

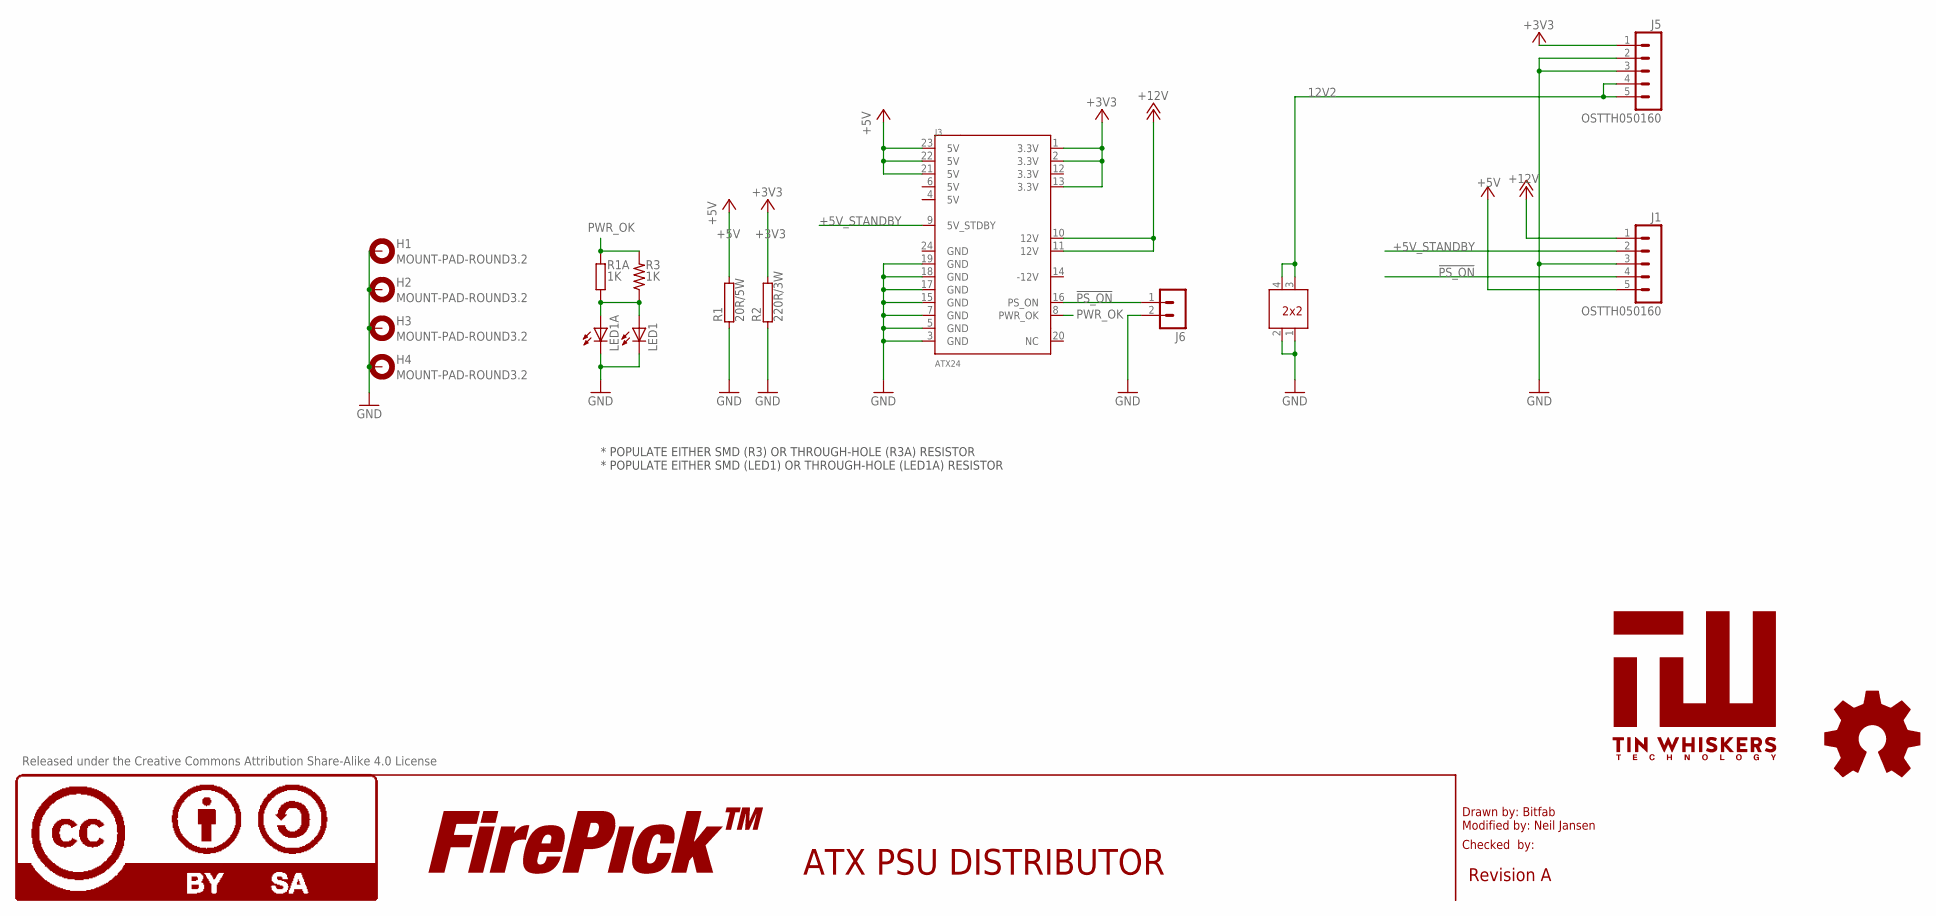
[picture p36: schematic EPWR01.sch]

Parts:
H1, H2, H3, H4: MOUNT-PAD-ROUND3.2; 3,2-PAD
J1, J5: OSTTH050160; CONN-OSTTH050160; PARTNO OSTTH050160
J3: ATX24; PARTNO 2-1586043-4
J4: ATX2X2; PARTNO 1586041-4
J6: MA02-1; PARTNO CONN-0.1-RA-1X2
LED1: LED1206; LED-1206; PARTNO LTST-C150AKT
LED1A: LED3MM; PARTNO *
LOGO4: LOGO-FIREPICKLARGE; LOGO-FIREPICK
LOGO5: LOGO-OSHWMEDIUM; LOGO-OSHW-MEDIUM
LOGO6: LOGO-CC-BY-SALARGE; LOGO-CC-BY-SA
R1: 20R/5W; HPS923; PARTNO SQP500JB-20R
R1A: 1K; 0207/10
R2: 220R/3W; CA4050; PARTNO PNP3WVJR-73-220R
R3: 1K; 0805; PARTNO RC0805FR-071KL
U$1: TIN-WHISKERSSMALL; TIN-WHISKERS-SMALL

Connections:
12V2: J4.3, J4.4, J5.4, J5.5
!PS_ON: J1.4, J3.16 (PS_ON), J6.1
+3V3: J3.1 (3.3V), J3.2 (3.3V), J3.13 (3.3V), J5.1, R2.2
+5V: J1.5, J3.21 (5V), J3.22 (5V), J3.23 (5V), R1.2
+5V_STANDBY: J1.2, J3.9 (5V_STDBY)
+12V: J1.1, J3.10 (12V), J3.11 (12V)
GND: H1.B3,2, H2.B3,2, H3.B3,2, H4.B3,2, J1.3, J3.3 (GND), J3.5 (GND), J3.7 (GND), J3.15 (GND), J3.17 (GND), J3.18 (GND), J3.19 (GND), J4.1, J4.2, J5.2, J5.3, J6.2, LED1.C, LED1A.K (C), R1.1, R2.1
unnamed: LED1.A, LED1A.A, R1A.1, R3.1
PWR_OK: J3.8 (PWR_OK), R1A.2, R3.2

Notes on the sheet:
Drawn by: Bitfab Modified by: Neil Jansen
Checked by:
Revision A
ATX PSU DISTRIBUTOR
Released under the Creative Commons Attribution Share-Alike 4.0 License
* POPULATE EITHER SMD (R3) OR THROUGH-HOLE (R3A) RESISTOR * POPULATE EITHER SMD (LED1) OR THROUGH-HOLE (LED1A) RESISTOR

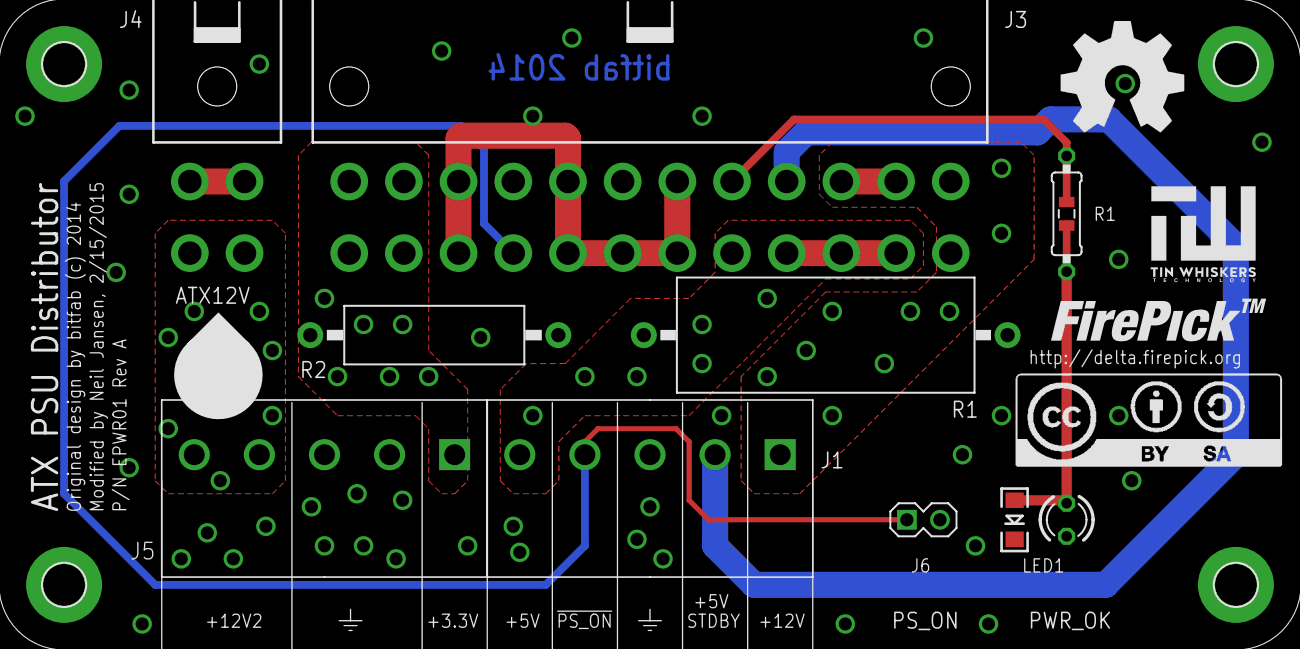
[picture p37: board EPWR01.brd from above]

Board: 2 copper layers, 21 parts (0 on the bottom side), 9 nets.

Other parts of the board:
U$5: REPRAP_BSTOP
U$6: OSHS_10X200_BSTOP

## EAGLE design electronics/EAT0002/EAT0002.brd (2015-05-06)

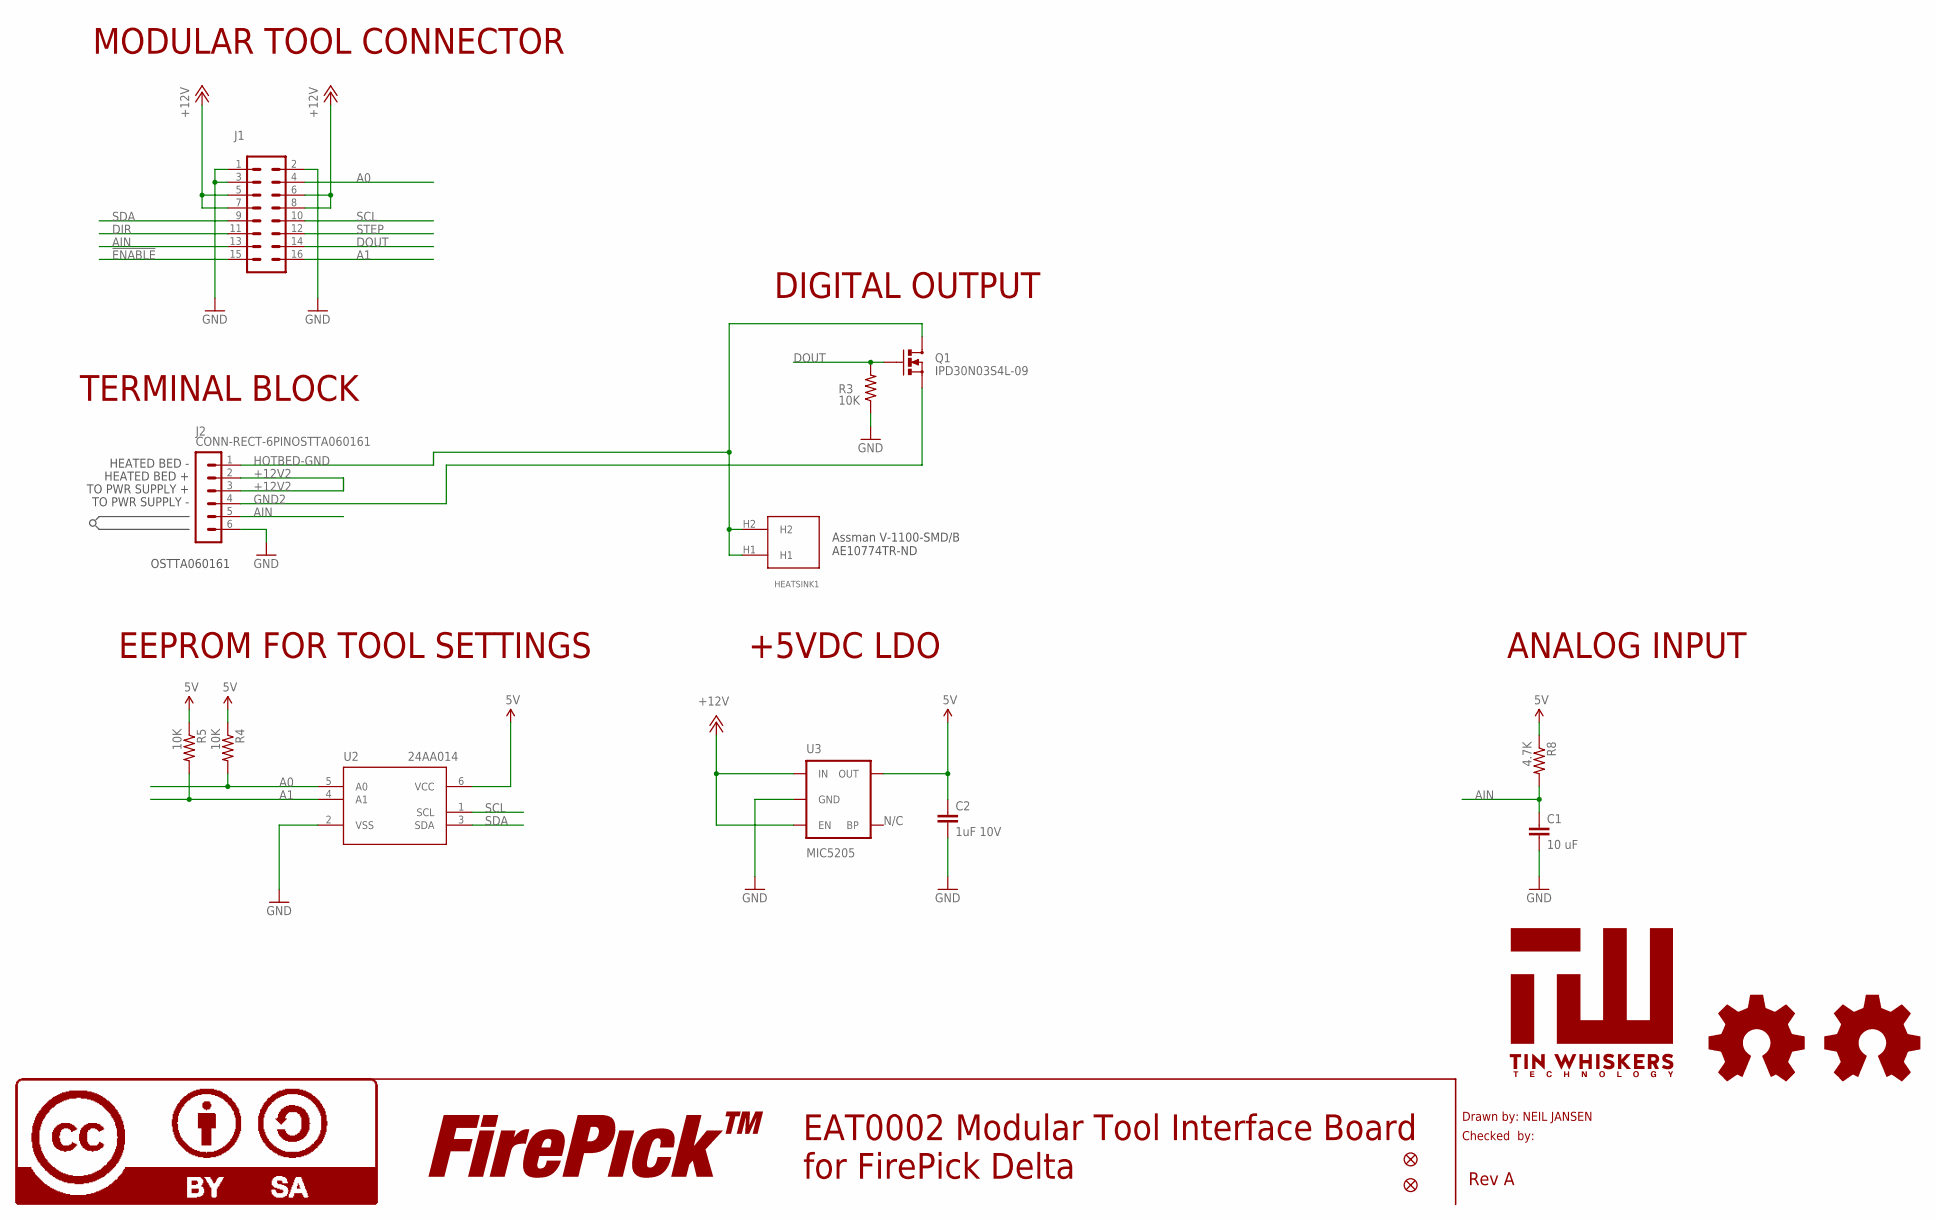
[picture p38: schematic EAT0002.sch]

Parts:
C1: 10 uF; 0805; PARTNO CC0805ZKY5V6BB106
C2: 1uF 10V; 0805; PARTNO CC0805KKX7R7BB105
FID1, FID2: FIDUCIAL
HEATSINK1: HEATSINK-DPAK; PARTNO V-1100-SMD/B
J1: CONN-RECT-16PIN-2ROWSIDE; CONN-RECT-2.54MM-16PIN-2ROW-SIDE; PARTNO CONN-0.1-S-2x8
J2: CONN-RECT-6PINOSTTA060161; CONN-OSTTA060161; PARTNO OSTTA060161
LOGO1, LOGO5: LOGO-OSHWSMALL; LOGO-OSHW-SMALL
LOGO4: LOGO-FIREPICKMEDIUM; LOGO-FIREPICK-MEDIUM
LOGO6: LOGO-CC-BY-SAMEDIUM; LOGO-CC-BY-SA-MEDIUM
Q1: IPD30N03S4L-09; DPAK; PARTNO IPD30N03S4L-09
R3, R4, R5: 10K; 0805; PARTNO RC0805FR-0710KL
R8: 4.7K; 0805; PARTNO RC0805FR-074K7L
U2: 24AA014; SOT23-6; PARTNO 24AA014T-I/OT
U3: MIC5205; SOT23-5; PARTNO MIC5205-5.0YM5 TR
U$1: TIN-WHISKERSSMALL; TIN-WHISKERS-SMALL

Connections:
5V: C2.1, R4.1, R5.1, R8.1, U2.6 (VCC), U3.5 (OUT)
!ENABLE: J1.15
+12V: J1.5, J1.6, J1.7, J1.8, U3.1 (IN), U3.3 (EN)
+12V2: J2.2, J2.3
A0: J1.4, R4.2, U2.5 (A0)
A1: J1.16, R5.2, U2.4 (A1)
AIN: C1.1, J1.13, J2.5, R8.2
DIR: J1.11
DOUT: J1.14, Q1.1 (G), R3.2
GND: C1.2, C2.2, J1.1, J1.2, J1.3, J2.6, R3.1, U2.2 (VSS), U3.2 (GND)
GND2: J2.4, Q1.3 (S)
HOTBED-GND: HEATSINK1.H1, HEATSINK1.H2, J2.1, Q1.4 (D)
SCL: J1.10, U2.1 (SCL)
SDA: J1.9, U2.3 (SDA)
STEP: J1.12

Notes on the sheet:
Drawn by: NEIL JANSEN
Checked by:
Rev A
EAT0002 Modular Tool Interface Board for FirePick Delta
MODULAR TOOL CONNECTOR
DIGITAL OUTPUT
EEPROM FOR TOOL SETTINGS
ANALOG INPUT
N/C
+5VDC LDO
TERMINAL BLOCK
OSTTA060161
Assman V-1100-SMD/B AE10774TR-ND
TO PWR SUPPLY -
TO PWR SUPPLY +
HEATED BED +
HEATED BED -

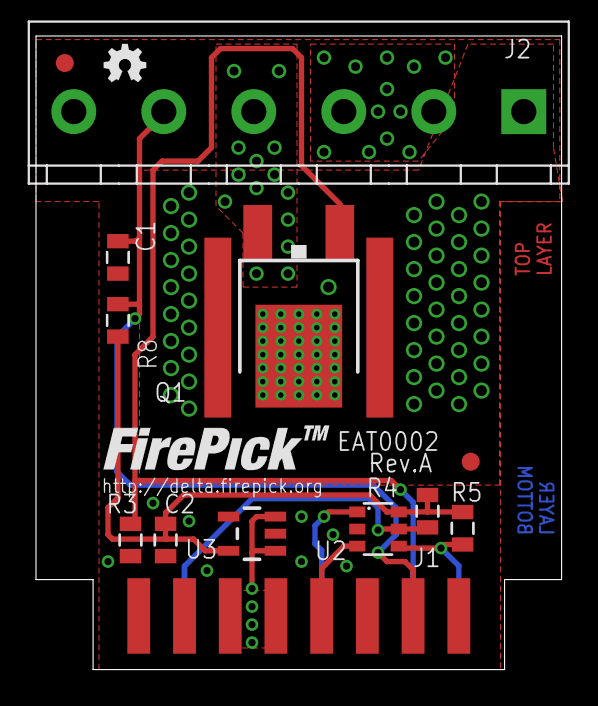
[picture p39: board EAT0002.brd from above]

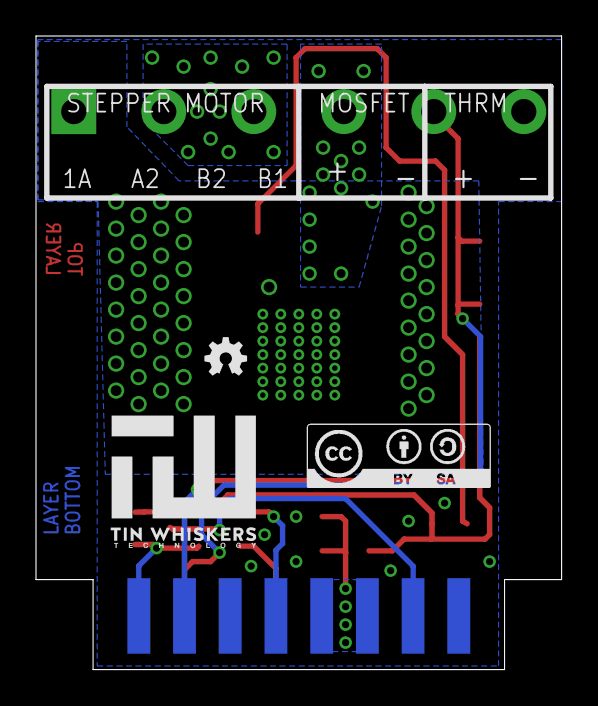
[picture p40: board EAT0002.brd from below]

Board: 2 copper layers, 29.2 x 35.2 mm, 19 parts (3 on the bottom side), 12 nets.

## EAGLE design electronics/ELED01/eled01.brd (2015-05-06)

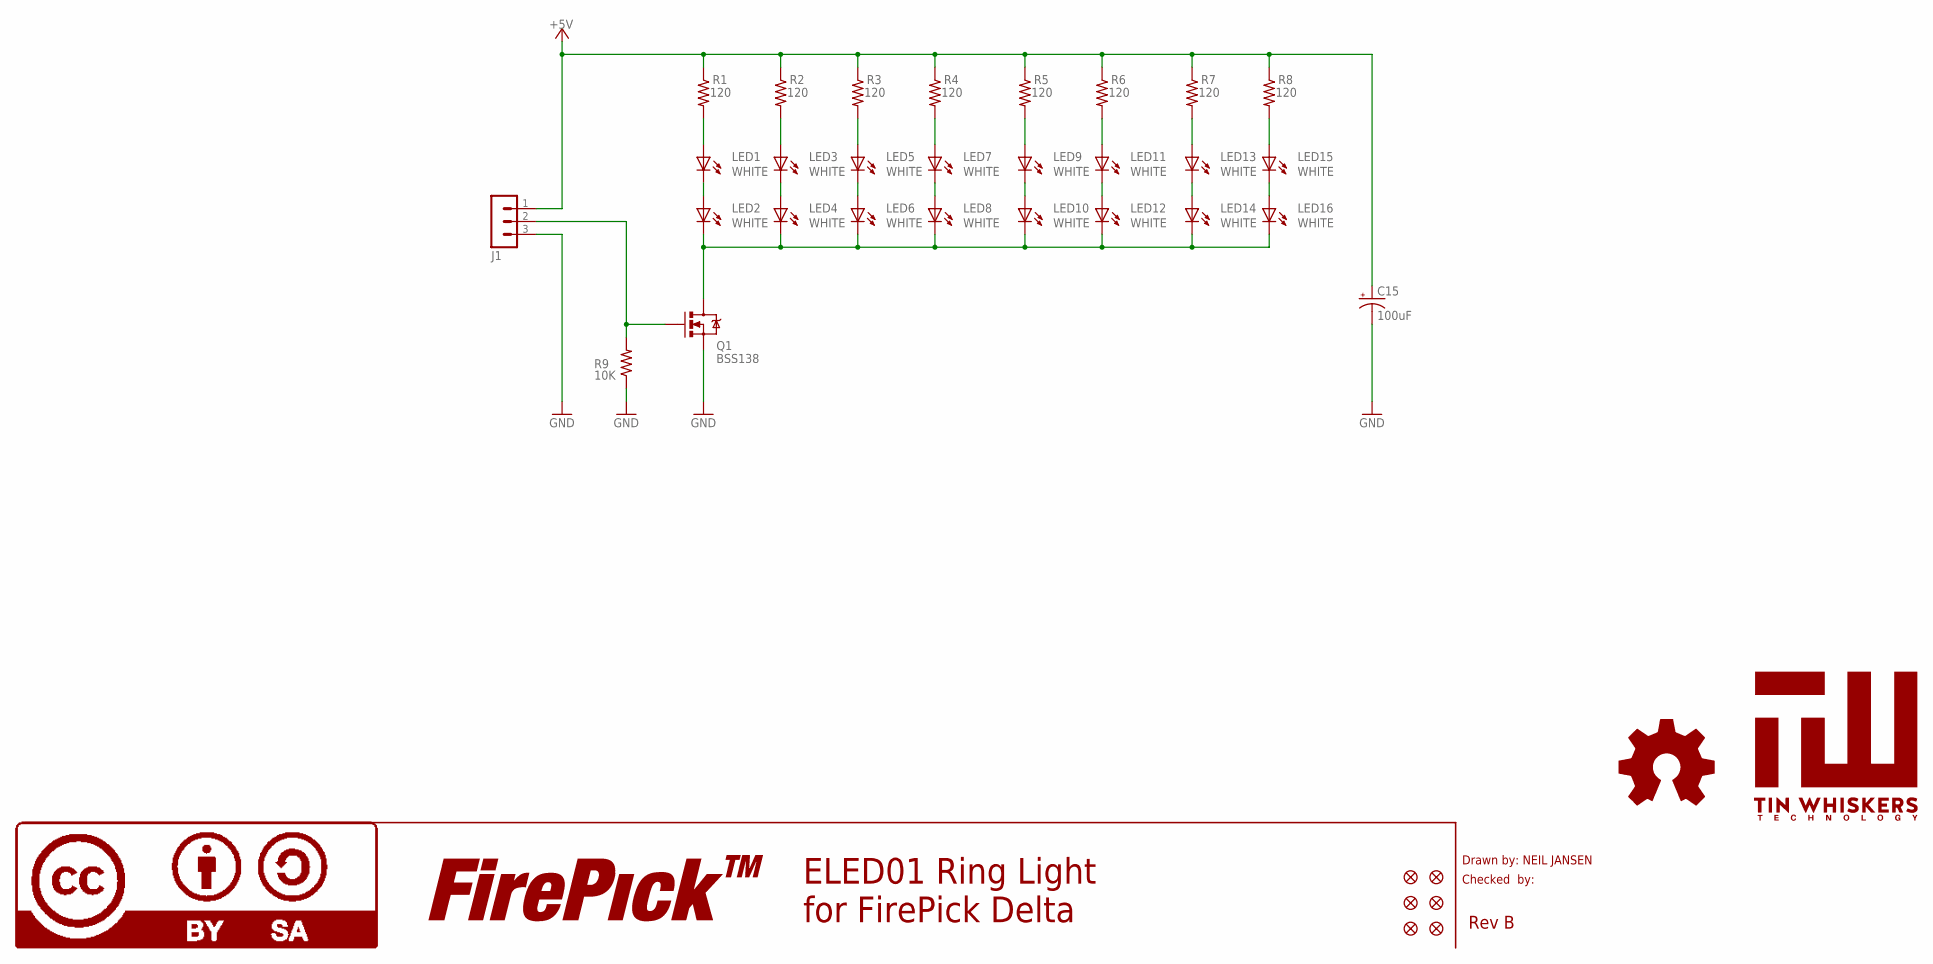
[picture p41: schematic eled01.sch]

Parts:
C15: 100uF; PANASONIC_D; PARTNO 25TXV100M6.3X8
FID1, FID2, FID3, FID4, FID5, FID6: FIDUCIAL
J1: MA03-1; PARTNO CONN-0.1-RA-1X3
LED1, LED2, LED3, LED4, LED5, LED6, LED7, LED8, LED9, LED10, LED11, LED12, LED13, LED14, LED15, LED16: WHITE; LED-1206-NO_SILK; PARTNO LTST-C150CKT
LOGO2: LOGO-OSHWSMALL; LOGO-OSHW-SMALL
LOGO4: LOGO-FIREPICKMEDIUM; LOGO-FIREPICK-MEDIUM
LOGO6: LOGO-CC-BY-SAMEDIUM; LOGO-CC-BY-SA-MEDIUM
Q1: BSS138; SOT23; PARTNO BSS138
R1, R2, R3, R4, R5, R6, R7, R8: 120; 0805; PARTNO RC0805FR-07120RL
R9: 10K; 0805; PARTNO RC0805FR-0710KL
U$1: TIN-WHISKERSSMALL; TIN-WHISKERS-SMALL

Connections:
+5V: C15.+, J1.1, R1.1, R2.1, R3.1, R4.1, R5.1, R6.1, R7.1, R8.1
DRAIN: LED2.C, LED4.C, LED6.C, LED8.C, LED10.C, LED12.C, LED14.C, LED16.C, Q1.3 (D)
ENABLE1: J1.2, Q1.1 (G), R9.2
GND: C15.-, J1.3, Q1.2 (S), R9.1
unnamed: LED1.C, LED2.A
unnamed: LED3.C, LED4.A
unnamed: LED7.C, LED8.A
unnamed: LED7.A, R4.2
unnamed: LED3.A, R2.2
unnamed: LED5.A, R3.2
unnamed: LED9.A, R5.2
unnamed: LED11.A, R6.2
unnamed: LED9.C, LED10.A
unnamed: LED5.C, LED6.A
unnamed: LED11.C, LED12.A
unnamed: LED13.C, LED14.A
unnamed: LED15.C, LED16.A
unnamed: LED13.A, R7.2
unnamed: LED15.A, R8.2
unnamed: LED1.A, R1.2

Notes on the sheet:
Drawn by: NEIL JANSEN
Checked by:
Rev B
ELED01 Ring Light for FirePick Delta

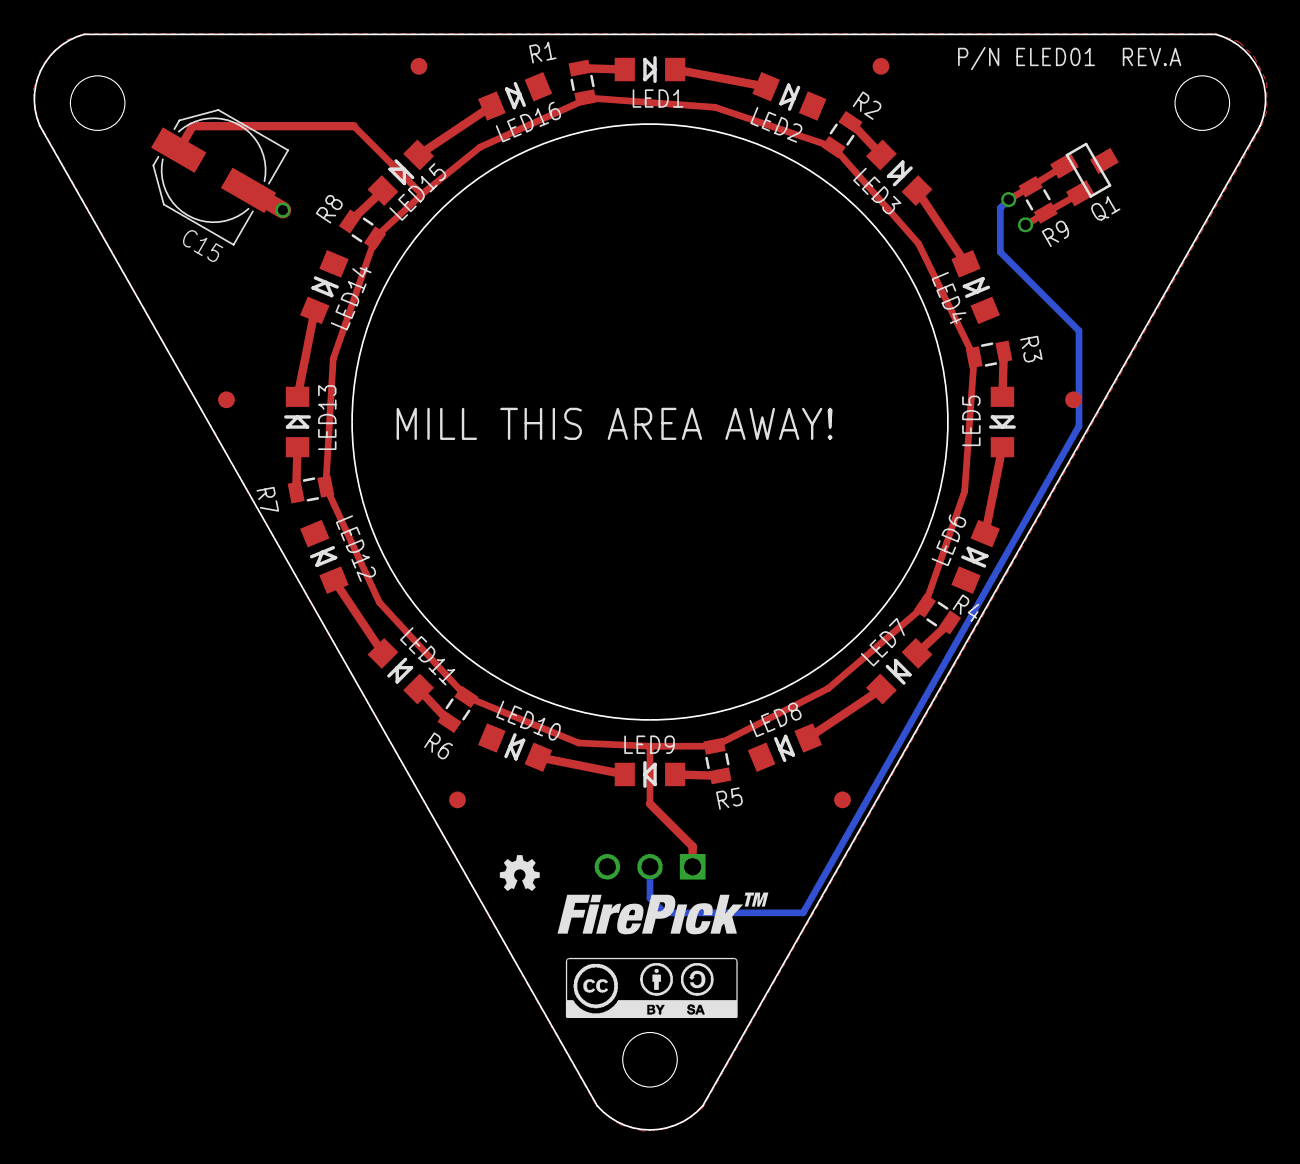
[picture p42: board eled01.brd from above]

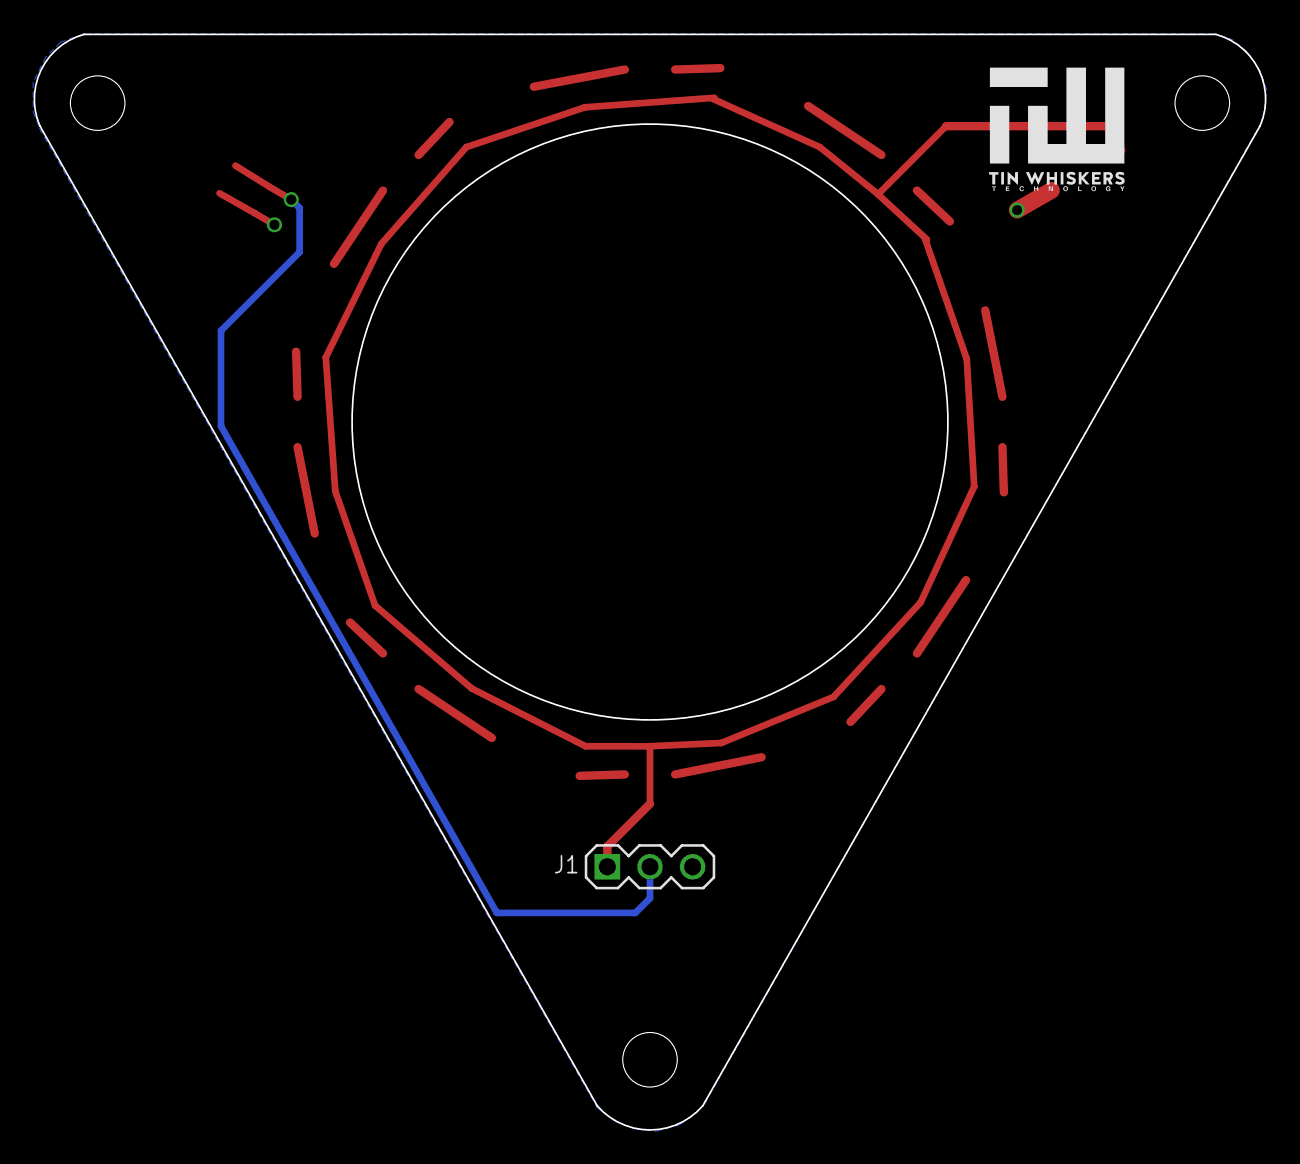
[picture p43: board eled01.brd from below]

Board: 2 copper layers, 73.4 x 65.3 mm, 38 parts (2 on the bottom side), 20 nets.

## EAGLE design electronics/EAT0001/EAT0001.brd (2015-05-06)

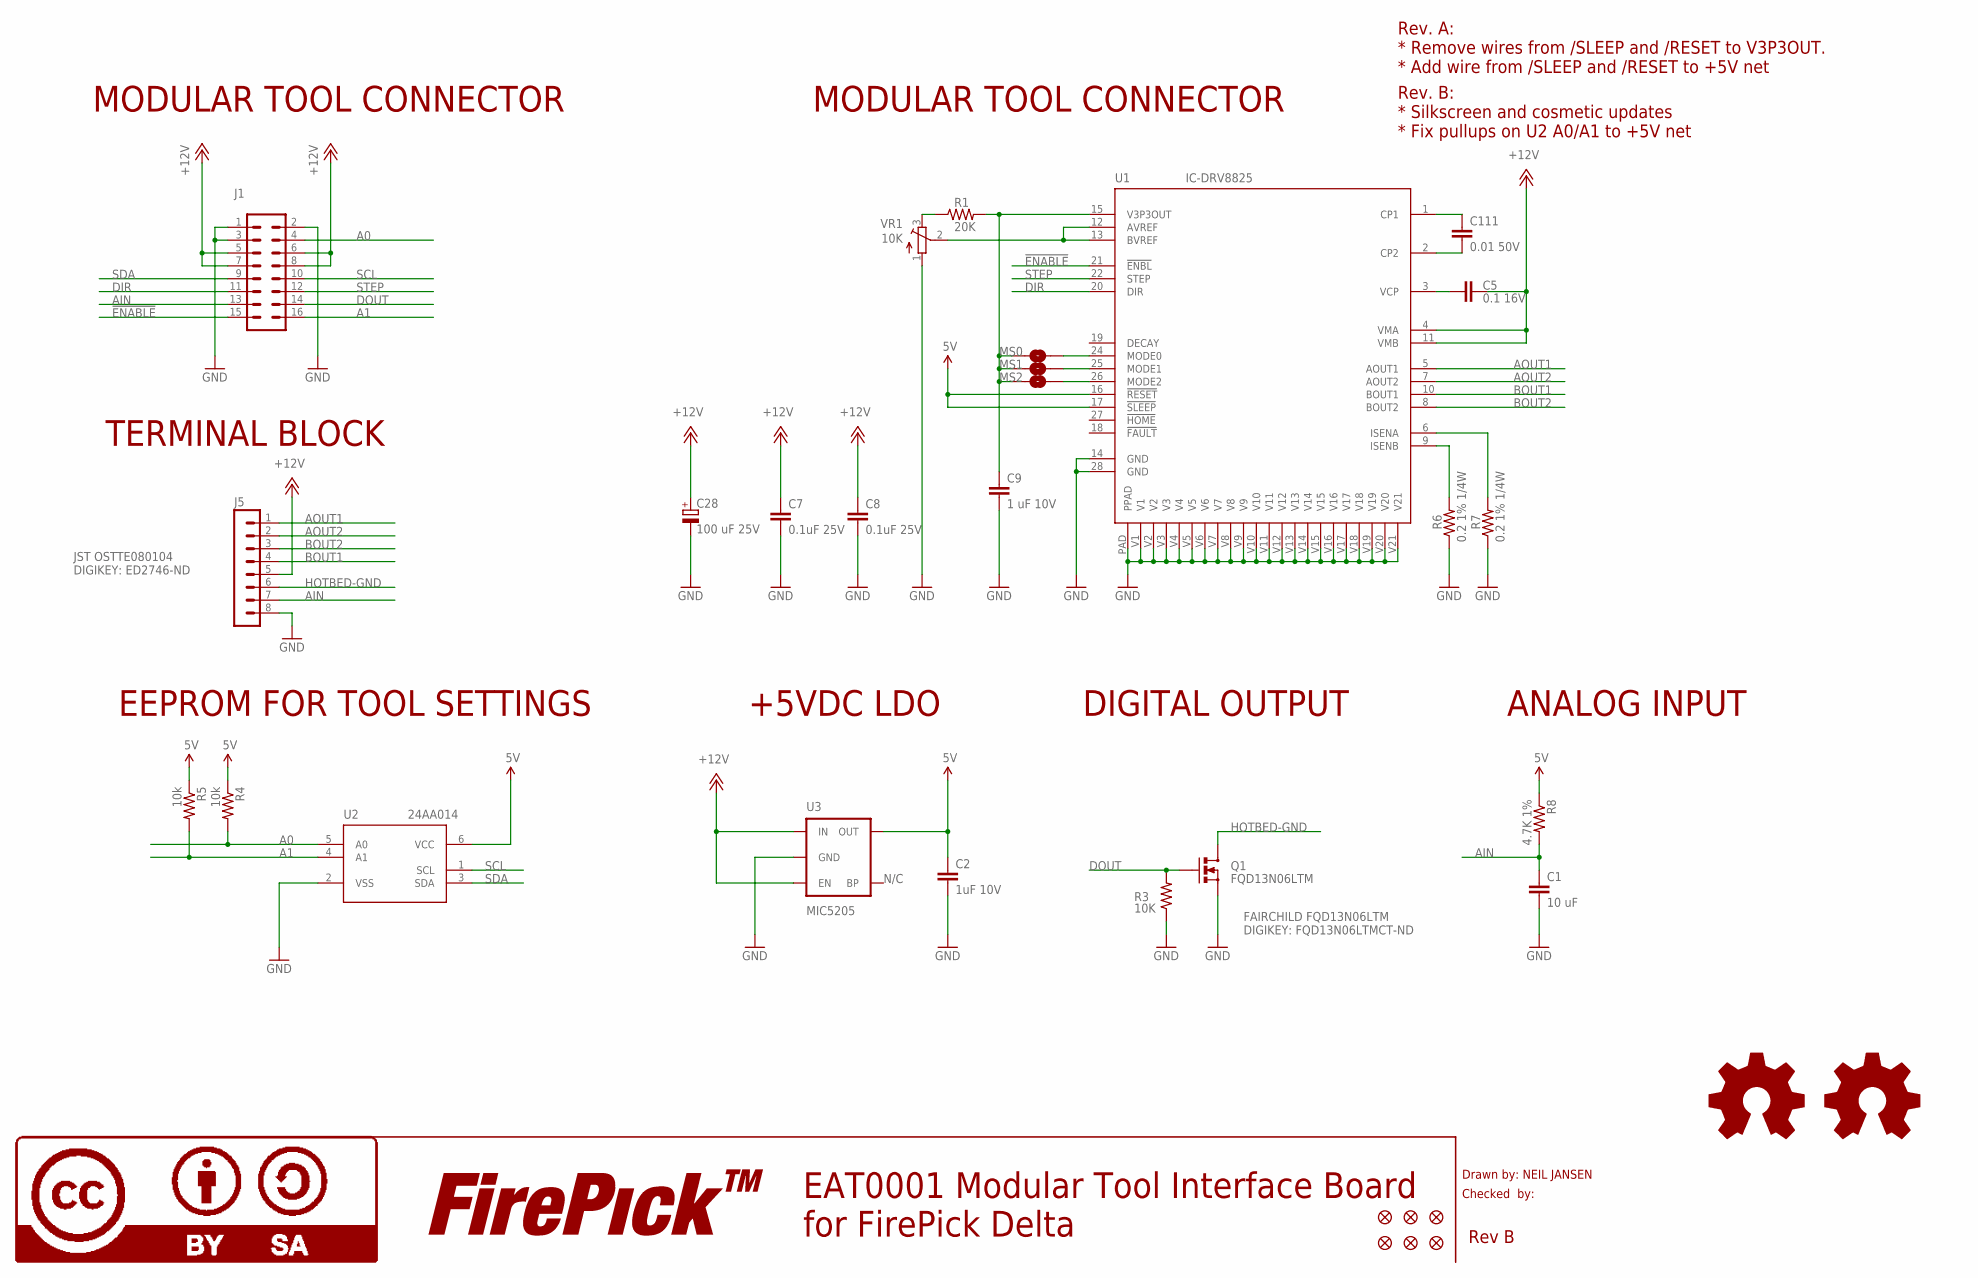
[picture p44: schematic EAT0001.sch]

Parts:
C1: 10 uF; 0805
C2: 1uF 10V; 0805
C5: 0.1 16V; 0805
C7, C8: 0.1uF 25V; 0805
C9: 1 uF 10V; 0805
C28: 100 uF 25V; UD-6,3X7,7_NICHICON
C111: 0.01 50V; 0805
FID1, FID2, FID3, FID4, FID5, FID6: FIDUCIAL1X2; FIDUCIAL-1X2
J1: CONN-RECT-16PIN-2ROWSIDE; CONN-RECT-2.54MM-16PIN-2ROW-SIDE
J5: CONN-OSTTE1201X4
LOGO1, LOGO5: LOGO-OSHWSMALL; LOGO-OSHW-SMALL
LOGO4: LOGO-FIREPICKMEDIUM; LOGO-FIREPICK-MEDIUM
LOGO6: LOGO-CC-BY-SAMEDIUM; LOGO-CC-BY-SA-MEDIUM
MS0, MS1, MS2: JUMPER; JUMPER-NC
Q1: FQD13N06LTM; DPAK
R1: 20K; 0805
R3: 10K; 0805
R4, R5: 10k; 0805
R6, R7: 0.2 1% 1/4W; 0805
R8: 4.7K 1%; 0805
U1: IC-DRV8825; TSSOP28_PAD
U2: 24AA014; SOT23-6
U3: MIC5205; SOT23-5
VR1: 10K; TC33X

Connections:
5V: C2.1, R4.1, R5.1, R8.1, U1.16 (!RESET), U1.17 (!SLEEP), U2.6 (VCC), U3.5 (OUT)
!ENABLE: J1.15, U1.21 (!ENBL)
+12V: C5.1, C7.1, C8.1, C28.+, J1.5, J1.6, J1.7, J1.8, J5.5, U1.4 (VMA), U1.11 (VMB), U3.1 (IN), U3.3 (EN)
A0: J1.4, R4.2, U2.5 (A0)
A1: J1.16, R5.2, U2.4 (A1)
AIN: C1.1, J1.13, J5.7, R8.2
AOUT1: J5.1, U1.5 (AOUT1)
AOUT2: J5.2, U1.7 (AOUT2)
BOUT1: J5.4, U1.10 (BOUT1)
BOUT2: J5.3, U1.8 (BOUT2)
CP1: C111.1, U1.1 (CP1)
CP2: C111.2, U1.2 (CP2)
DIR: J1.11, U1.20 (DIR)
DOUT: J1.14, Q1.1 (G), R3.2
GND: C1.2, C2.2, C7.2, C8.2, C9.2, C28.-, J1.1, J1.2, J1.3, J5.8, Q1.3 (S), R3.1, R6.1, R7.1, U1.14 (GND), U1.28 (GND), U1.PAD, U1.V1, U1.V2, U1.V3, U1.V4, U1.V5, U1.V6, U1.V7, U1.V8, U1.V9, U1.V10, U1.V11, U1.V12, U1.V13, U1.V14, U1.V15, U1.V16, U1.V17, U1.V18, U1.V19, U1.V20, U1.V21, U2.2 (VSS), U3.2 (GND), VR1.1 (A)
HOTBED-GND: J5.6, Q1.4 (D)
ISENA: R7.2, U1.6 (ISENA)
ISENB: R6.2, U1.9 (ISENB)
MOD1: MS1.2, U1.25 (MODE1)
MODE0: MS0.2, U1.24 (MODE0)
MODE2: MS2.2, U1.26 (MODE2)
unnamed: R1.1, VR1.3 (E)
SCL: J1.10, U2.1 (SCL)
SDA: J1.9, U2.3 (SDA)
STEP: J1.12, U1.22 (STEP)
V3P3OUT: C9.1, MS0.1, MS1.1, MS2.1, R1.2, U1.15 (V3P3OUT)
VCP: C5.2, U1.3 (VCP)
VREF: U1.12 (AVREF), U1.13 (BVREF), VR1.2 (S)

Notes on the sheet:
Drawn by: NEIL JANSEN
Checked by:
Rev B
EAT0001 Modular Tool Interface Board for FirePick Delta
MODULAR TOOL CONNECTOR
DIGITAL OUTPUT
EEPROM FOR TOOL SETTINGS
ANALOG INPUT
N/C
+5VDC LDO
JST OSTTE080104 DIGIKEY: ED2746-ND
TERMINAL BLOCK
FAIRCHILD FQD13N06LTM DIGIKEY: FQD13N06LTMCT-ND
Rev. A: * Remove wires from /SLEEP and /RESET to V3P3OUT. * Add wire from /SLEEP and /RESET to +5V net
Rev. B: * Silkscreen and cosmetic updates * Fix pullups on U2 A0/A1 to +5V net



Board: 4 copper layers, 29.2 x 33.2 mm, 35 parts (16 on the bottom side), 28 nets.

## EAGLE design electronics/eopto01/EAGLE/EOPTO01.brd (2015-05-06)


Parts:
FID3, FID4: FIDUCIAL1X2; FIDUCIAL-1X2
J1: CONN-0.1-S-1X3; MA03-1; PARTNO CONN-0.1-RA-1X3
LED1: AMBER; LED-1206; PARTNO LTST-C150AKT
LOGO4: LOGO-FIREPICKMEDIUM; LOGO-FIREPICK-MEDIUM
LOGO5: LOGO-OSHWSMALL; LOGO-OSHW-SMALL
LOGO6: LOGO-CC-BY-SAMEDIUM; LOGO-CC-BY-SA-MEDIUM
OPTO1: TCST2103; TCST2013; PARTNO TCST2103
Q2: BSS138; SOT23; PARTNO BSS138
R1: 120; 0805; PARTNO RC0805FR-07120RL
R2: 10k; 0805; PARTNO RC0805FR-0710KL
R3: 1k; 0805; PARTNO RC0805FR-071KL

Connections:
5V: J1.1, R1.2, R2.2, R3.2
GND: J1.3, OPTO1.LED_K, OPTO1.NPN_E, Q2.2 (S)
unnamed: LED1.C, Q2.3 (D)
unnamed: LED1.A, R3.1
unnamed: OPTO1.LED_A, R1.1
OPTO_OUT: J1.2, OPTO1.NPN_C, Q2.1 (G), R2.1

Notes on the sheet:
Drawn by: NEIL JANSEN
Checked by:
v0.1
EAT0001 Modular Tool Interface Board for FirePick Delta


Board: 2 copper layers, 33.0 x 11.0 mm, 12 parts (1 on the bottom side), 6 nets.

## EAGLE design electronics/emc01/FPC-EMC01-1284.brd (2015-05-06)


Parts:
C1, C5, C7, C8: 0.1 uF; 0805
C2, C15, C16, C17: 100uF; PANASONIC_D
C3, C11: 22P; 0805
C4, C6, C9, C10, C14: 0.1uF; 0805
C12, C13: 47pF; 0805
FID1, FID2, FID3, FID4: FIDUCIAL1X2; FIDUCIAL-1X2
J1: USB-MINIB-5PIN; USB-MINIB
J3: DNP; MA06-1
J4, J5, J6: MA04-1
J4A: MOT-X; CONN-JST-PH_2.0MM_4PIN-SMT-RA
J5A: MOT-Y; CONN-JST-PH_2.0MM_4PIN-SMT-RA
J6A: MOT-Z; CONN-JST-PH_2.0MM_4PIN-SMT-RA
J7, J8, J9: MA03-1
J7A, J8A, J9A: CONN-RECT-3PINJST_PH_2MM; CONN-JST_PH-2.0MM-3PIN-SMT-RA
J10: CONN-OSTTA020161
J11, J12, J13, J14: CONN-RECT-16PIN-2ROW; CONN-RECT-2.54MM-16PIN-2ROW-SMTH
J15: DNP; MA04-1
J16: ICSP; CONN-RECT-2.54MM-6-PIN-2ROW-SMTH
LED1: Green; LED-1206-NO_SILK
LED2: Red; LED-1206-NO_SILK
LED3: Yellow; LED-1206-NO_SILK
LOGO4: LOGO-FIREPICK
LOGO5: LOGO-OSHWMEDIUM; LOGO-OSHW-MEDIUM
LOGO6: LOGO-CC-BY-SA
Q2: 2N7002PW; SOT323
R1, R2: 10K; 0805
R3, R4, R5, R6, R7: 1k; 0805
R8, R9: 27; 0805
R10, R11: 10k; 0805
R12, R13: 4.7K; 0805
S1: TAC_SWITCHSMD; TACTILE_SWITCH_SMD
STEPSTICK1, STEPSTICK2, STEPSTICK3: STEPSTICK
TP1: PD2; CON-TESTPOINT
TP2: +12V; CON-TESTPOINT
TP3: GND; CON-TESTPOINT
TP4: +5V; CON-TESTPOINT
TP5: +3.3V; CON-TESTPOINT
U1: IC-ATMEGA1284P-AU; QFP44
U2: FT231XS; SSOP20_L
U3: V_REG_LM1117SOT223; SOT223
X1: 16Mhz; CTS406

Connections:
3.3V: C10.1, Q2.1 (G), R10.2, TP5.1, U2.3 (VCCIO), U2.13 (3V3OUT), U2.14 (!RESET)
12V: C14.1, C15.+, C16.+, C17.+, J10.2, J11.5, J11.6, J11.7, J11.8, J12.5, J12.6, J12.7, J12.8, J13.5, J13.6, J13.7, J13.8, J14.5, J14.6, J14.7, J14.8, STEPSTICK1.VMOT, STEPSTICK2.VMOT, STEPSTICK3.VMOT, TP2.1, U3.3 (IN)
!RESET: C9.2, J16.2, R1.1, S1.3, S1.4, U1.4 (!RESET)
!XYZ_ENABLE: R2.1, STEPSTICK1.!ENABLE!, STEPSTICK2.!ENABLE!, STEPSTICK3.!ENABLE!, U1.15 ((PCINT30/OC2B/ICP)PD6)
+5V: C1.1, C2.+, C5.1, C6.1, C7.1, C8.1, J3.4, J7.2, J7A.2, J8.2, J8A.2, J9.2, J9A.2, J15.1, J16.5, R1.2, R2.2, R3.2, R4.1, R5.1, R11.2, R12.2, R13.2, STEPSTICK1.MS1, STEPSTICK1.MS2, STEPSTICK1.MS3, STEPSTICK1.VDD, STEPSTICK2.MS1, STEPSTICK2.MS2, STEPSTICK2.MS3, STEPSTICK2.VDD, STEPSTICK3.MS1, STEPSTICK3.MS2, STEPSTICK3.MS3, STEPSTICK3.VDD, TP4.1, U1.5 (VCC), U1.17 (VCC), U1.27 (AVCC), U1.38 (VCC), U2.15 (VCC), U3.2 (OUT), U3.4 (OUT)
AREF: C4.1, U1.29 (AREF)
AVR_RXD: J3.3, R6.1, U1.9 ((PCINT24/RXD0/T3*)PD0)
AVR_TXD: J3.2, R7.1, U1.10 ((PCINT25/TXD0)PD1)
D+: C13.1, J1.D+, R9.1
D-: C12.1, J1.D-, R8.1
DTR: C9.1, J3.1, Q2.3 (D), R11.1
DTR_3.3V: Q2.2 (S), R10.1, U2.1 (!DTR)
GND: C1.2, C2.-, C3.2, C4.2, C5.2, C6.2, C7.2, C8.2, C10.2, C11.2, C12.2, C13.2, C14.2, C15.-, C16.-, C17.-, J1.GND, J1.MTN1 (MTN2), J1.MTN2 (MTN3), J1.MTN3 (MTN1), J1.MTN4, J3.5, J3.6, J7.3, J7A.3, J8.3, J8A.3, J9.3, J9A.3, J10.1, J11.1, J11.2, J11.3, J11.16, J12.1, J12.2, J12.3, J12.4, J13.1, J13.2, J13.3, J13.4, J13.16, J14.1, J14.2, J14.3, J15.2, J16.1, LED1.C, S1.1, S1.2, STEPSTICK1.GND, STEPSTICK1.GND@2 (GND), STEPSTICK2.GND, STEPSTICK2.GND@2 (GND), STEPSTICK3.GND, STEPSTICK3.GND@2 (GND), TP3.1, U1.6 (GND), U1.18 (GND), U1.28 (GND), U1.39 (GND), U2.6 (GND), U2.16 (GND), U3.1 (ADJ)
MISO: J16.6, U1.2 (PB6(PCINT14/OC3A/MISO))
MOSI: J16.3, U1.1 (PB5(PCINT13/ICP3/MOSI))
unnamed: LED1.A, R3.1
unnamed: STEPSTICK1.!RESET!, STEPSTICK1.!SLEEP!
unnamed: STEPSTICK2.!RESET!, STEPSTICK2.!SLEEP!
unnamed: LED2.A, R4.2
unnamed: LED3.A, R5.2
unnamed: R8.2, U2.12 (USBDM)
unnamed: STEPSTICK3.!RESET!, STEPSTICK3.!SLEEP!
unnamed: R9.2, U2.11 (USBDP)
RXD: R7.2, U2.4 (RXD)
RXLED: LED3.C, U2.17 (CBUS1)
SCL: J11.10, J12.10, J13.10, J14.10, J15.3, R12.1, U1.19 ((SCL/PCINT16)PC0)
SCLK: J16.4, U1.3 (PB7(PCINT15/OC3B/SCK))
SDA: J11.9, J12.9, J13.9, J14.9, J15.4, R13.1, U1.20 ((SDA/PCINT17)PC1)
SPARE: TP1.1, U1.11 ((PCINT26/RXD1/INT0)PD2)
TOOL1_AIN: J11.13, U1.37 (PA0(ADC0/PCINT0))
TOOL1_DOUT: J11.14, U1.36 (PA1(ADC1/PCINT1))
TOOL1_ENABLE: J11.15, U1.41 (PB1(PCINT9/CLKO/T1))
TOOL2_AIN: J12.13, U1.35 (PA2(ADC2/PCINT2))
TOOL2_DOUT: J12.14, U1.34 (PA3(ADC3/PCINT3))
TOOL2_ENABLE: J12.15, U1.40 (PB0(PCINT8/XCK0/T0))
TOOL3_AIN: J13.13, U1.32 (PA5(ADC5/PCINT5))
TOOL3_DOUT: J13.14, U1.33 (PA4(ADC4/PCINT4))
TOOL3_ENABLE: J13.15, U1.22 ((TMS/PCINT19)PC3)
TOOL4_AIN: J14.13, U1.30 (PA7(ADC7/PCINT7))
TOOL4_DOUT: J14.14, U1.31 (PA6(ADC6/PCINT6))
TOOL4_ENABLE: J14.15, U1.21 ((TCK/PCINT18)PC2)
TOOL_DIR: J11.11, J12.11, J13.11, J14.11, U1.16 ((OC2A/PCINT31)PD7)
TOOL_STEP: J11.12, J12.12, J13.12, J14.12, U1.23 ((TDO/PCINT20)PC4)
TXD: R6.2, U2.20 (TXD)
TXLED: LED2.C, U2.10 (CBUS2)
X1A: J4.2, J4A.2, STEPSTICK1.1A
X1B: J4.1, J4A.1, STEPSTICK1.1B
X2A: J4.3, J4A.3, STEPSTICK1.2A
X2B: J4.4, J4A.4, STEPSTICK1.2B
XTAL1: C3.1, U1.8 (XTAL1), X1.3 (2)
XTAL2: C11.1, U1.7 (XTAL2), X1.1
X_DIR: STEPSTICK1.DIR, U1.25 ((TOSC1/PCINT22)PC6)
X_STEP: STEPSTICK1.STEP, U1.26 ((TOSC2/PCINT23)PC7)
X_STOP: J7.1, J7A.1, U1.24 ((TDI/PCINT21)PC5)
Y1A: J5.2, J5A.2, STEPSTICK2.1A
Y1B: J5.1, J5A.1, STEPSTICK2.1B
Y2A: J5.3, J5A.3, STEPSTICK2.2A
Y2B: J5.4, J5A.4, STEPSTICK2.2B
Y_DIR: STEPSTICK2.DIR, U1.43 (PB3(PCINT11/OC0A/AIN1))
Y_STEP: STEPSTICK2.STEP, U1.44 (PB4(PCINT12/OC0B/SS))
Y_STOP: J8.1, J8A.1, U1.42 (PB2(PCINT10/INT2/AIN0))
Z1A: J6.2, J6A.2, STEPSTICK3.1A
Z1B: J6.1, J6A.1, STEPSTICK3.1B
Z2A: J6.3, J6A.3, STEPSTICK3.2A
Z2B: J6.4, J6A.4, STEPSTICK3.2B
Z_DIR: STEPSTICK3.DIR, U1.13 ((PCINT28/XCK1/OC1B)PD4)
Z_STEP: STEPSTICK3.STEP, U1.14 ((PCINT29/OC1A)PD5)
Z_STOP: J9.1, J9A.1, U1.12 ((PCINT27/TXD1/INT1)PD3)

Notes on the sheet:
I2C ADDRESS MAP: A1 A0 00: TOOL#3 01: TOOL#2 10: TOOL#1 11: TOOL#4
MODULAR TOOL #4
MODULAR TOOL #3
MODULAR TOOL #2
MODULAR TOOL #1
5V (FTDI Passthru header, provision for FTDI driver but do not populate for cost reduction)
Drawn by: NEIL JANSEN
Checked by:
Revision C
EMC01 Motion Controller for FirePick Delta
ATMEL ATMEGA1284P-AU
FT231X USB-TO-TTL SERIAL
X AXIS STEPPER DRIVER
ENDSTOPS
MODULAR TOOL SYSTEM
FTDI SERIAL HEADER
+12VDC IN
ICSP
I2C
TEST POINTS
N/C
Y AXIS STEPPER DRIVER
Z AXIS STEPPER DRIVER
Released under the Creative Commons Attribution Share-Alike 4.0 License
VREG
Revision A: First official release. Revision B: Added voltage regulator. Moved vias. Updated silkscreen. Revision C: Fixed air-wire @ C3/C11 to GND (Thanks, Douglas!)


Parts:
U4: IC-ATMEGA1284P-AU; QFP44

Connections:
AVCC: U4.27 (AVCC)
VCC: U4.5 (VCC), U4.17 (VCC), U4.38 (VCC)

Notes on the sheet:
ARDUINO PIN MAPPING -----------------------------------------


Board: 2 copper layers, 100.0 x 86.6 mm, 76 parts (0 on the bottom side), 69 nets.

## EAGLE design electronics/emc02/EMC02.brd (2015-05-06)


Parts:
ARDUINO: ARDUINO-MEGA; PARTNO CONN-0.1-ARD-2560
C8, C9, C10, C11, C15, C16, C17: 100uF; PANASONIC_D; PARTNO 25TXV100M6.3X8
D1: 1N4148; SOD-123; PARTNO 1N4148W-7-F
FID1, FID2, FID3, FID4, FID5, FID6, FID7: FIDUCIAL
IC1, IC2: 74ACT244DW; SO20W; PARTNO 74ACT244SCX
J4, J5, J6: CONN-0.1-RA-1X4; MA04-1; PARTNO CONN-0.1-RA-1X4
J4A: MOT-X; CONN-JST-PH_2.0MM_4PIN-SMT-RA
J5A: MOT-Y; CONN-JST-PH_2.0MM_4PIN-SMT-RA
J6A: MOT-Z; CONN-JST-PH_2.0MM_4PIN-SMT-RA
J11, J12, J13, J14: CONN-RECT-16PIN-2ROW; CONN-RECT-2.54MM-16PIN-2ROW-SMTH; PARTNO PPPC081LFBN-RC
J18, J19, J20: CONN-0.1-S-2X3; MA03-2; PARTNO CONN-0.1-S-2X3
J24, J25, J26, J28: CONN-0.1-S-1X3; MA03-1; PARTNO CONN-0.1-S-1X3
J31: CONN-0.1-S-1X2; MA02-1; PARTNO CONN-0.1-S-1X2
LOGO4: LOGO-FIREPICKLARGE; LOGO-FIREPICK
LOGO5: LOGO-OSHWMEDIUM; LOGO-OSHW-MEDIUM
LOGO6: LOGO-CC-BY-SALARGE; LOGO-CC-BY-SA
R1, R6, R7, R29: 100K; 0805; PARTNO RC0805FR-07100KL
R2, R8, R9, R12, R13, R16, R18, R30, R31, R32, R33, R40, R41, R42, R43: 10K; 0805; PARTNO RC0805FR-0710KL
R19, R22, R23, R24: 20K; 0805; PARTNO RC0805FR-0720KL
R28: 4.7K; 0805; PARTNO RC0805FR-074K7L
STEPSTICK1, STEPSTICK2, STEPSTICK3: STEPSTICK; PARTNO PPPC081LFBN-RC
U$25: TIN-WHISKERSTSTOP; TIN-WHISKERS-TSTOP

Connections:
3.3V: ARDUINO.3.3V; also elsewhere on the board
12V: C8.+, C9.+, C10.+, C11.+, C15.+, C16.+, C17.+, J11.5, J11.6, J11.7, J11.8, J12.5, J12.6, J12.7, J12.8, J13.5, J13.6, J13.7, J13.8, J14.5, J14.6, J14.7, J14.8, STEPSTICK1.VMOT, STEPSTICK2.VMOT, STEPSTICK3.VMOT; also elsewhere on the board
20_SDA: ARDUINO.20 (20(SDA)); also elsewhere on the board
21_SCL: ARDUINO.21 (21(SCL)); also elsewhere on the board
!PS_ON_BUF: ARDUINO.28; also elsewhere on the board
!RESET: ARDUINO.ICSP-RESET, ARDUINO.RESET; also elsewhere on the board
!TOOL1_ENABLE: IC1.9 (Y1), J11.15, R43.2
!TOOL1_EN_BUF: ARDUINO.44, IC1.11 (A1)
!TOOL2_ENABLE: IC1.7 (Y2), J12.15, R42.2
!TOOL2_EN_BUF: ARDUINO.52, IC1.13 (A2)
!TOOL3_ENABLE: IC1.5 (Y3), J13.15, R41.2
!TOOL3_EN_BUF: ARDUINO.24, IC1.15 (A3)
!TOOL4_ENABLE: IC1.3 (Y4), J14.15, R40.2
!TOOL4_EN_BUF: ARDUINO.34, IC1.17 (A4)
!X_ENABLE: IC1.18 (Y1), R2.1, STEPSTICK1.!ENABLE!
!X_ENABLE_BUF: ARDUINO.40, IC1.2 (A1)
!Y_ENABLE: IC1.16 (Y2), R8.1, STEPSTICK2.!ENABLE!
!Y_ENABLE_BUF: ARDUINO.A0 (A0(RX0)), IC1.4 (A2)
!Z_ENABLE: IC1.14 (Y3), R9.1, STEPSTICK3.!ENABLE!
!Z_ENABLE_BUF: ARDUINO.2, IC1.6 (A3)
+5V: J18.2, J18.4, J18.6, J19.2, J19.4, J19.6, J20.2, J20.4, J20.6, R2.2, R8.2, R9.2, R40.1, R41.1, R42.1, R43.1, STEPSTICK1.VDD, STEPSTICK2.VDD, STEPSTICK3.VDD; also elsewhere on the board
AVR_RXD: ARDUINO.0 (0(RX0)); also elsewhere on the board
AVR_TXD: ARDUINO.1 (1(TX0)); also elsewhere on the board
D13_LED: ARDUINO.13; also elsewhere on the board
ESTOP: ARDUINO.12, D1.C
ESTOP_OE: D1.A, IC1.1 (G), IC1.19 (G), IC2.19 (G), J31.2, R29.1
FAN2_PWM: ARDUINO.10; also elsewhere on the board
FAN2_TACH: ARDUINO.11; also elsewhere on the board
GND: ARDUINO.GND@0 (GND), ARDUINO.GND@1 (GND), ARDUINO.GND@2 (GND), ARDUINO.GND@3 (GND), ARDUINO.GND@4 (GND), ARDUINO.ICSP-GND, C8.-, C9.-, C10.-, C11.-, C15.-, C16.-, C17.-, IC1.8 (A4), IC2.1 (G), J11.1, J11.2, J11.3, J11.16, J12.1, J12.2, J12.3, J12.4, J13.1, J13.2, J13.3, J13.4, J13.16, J14.1, J14.2, J14.3, R1.1, R6.1, R7.1, R19.1, R22.1, R23.1, R24.1, R28.1, R30.1, R31.1, R32.1, R33.1, STEPSTICK1.GND, STEPSTICK1.GND@2 (GND), STEPSTICK2.GND, STEPSTICK2.GND@2 (GND), STEPSTICK3.GND, STEPSTICK3.GND@2 (GND); also elsewhere on the board
IOREF: ARDUINO.IOREF, R29.2; also elsewhere on the board
ISENSE: ARDUINO.A8; also elsewhere on the board
MISO: ARDUINO.ICSP-MISO (ISCP-MISO); also elsewhere on the board
MOSI: ARDUINO.ICSP-MOSI; also elsewhere on the board
unnamed: J31.1, R28.2
unnamed: J24.3, R22.2
unnamed: J28.3, R19.2
unnamed: STEPSTICK1.!RESET!, STEPSTICK1.!SLEEP!
unnamed: J25.3, R23.2
unnamed: J26.3, R24.2
unnamed: STEPSTICK2.!RESET!, STEPSTICK2.!SLEEP!
unnamed: STEPSTICK3.!RESET!, STEPSTICK3.!SLEEP!
RX1: ARDUINO.19 (19(RX1)); also elsewhere on the board
RX2: ARDUINO.17 (17(RX2)); also elsewhere on the board
RX3: ARDUINO.15 (15(RX3)); also elsewhere on the board
SCL: ARDUINO.SCL; also elsewhere on the board
SCLK: ARDUINO.ICSP-SCK; also elsewhere on the board
SDA: ARDUINO.SDA; also elsewhere on the board
SERVO1: IC2.18 (Y1); also elsewhere on the board
SERVO1_BUF: ARDUINO.4, IC2.2 (A1)
SERVO2: IC2.16 (Y2); also elsewhere on the board
SERVO2_BUF: ARDUINO.5, IC2.4 (A2)
SERVO3: IC2.14 (Y3); also elsewhere on the board
SERVO3_BUF: ARDUINO.6, IC2.6 (A3)
SERVO4: IC2.12 (Y4); also elsewhere on the board
SERVO4_BUF: ARDUINO.7, IC2.8 (A4)
SPAREIO_0: ARDUINO.23; also elsewhere on the board
SPAREIO_1: ARDUINO.25; also elsewhere on the board
SPAREIO_2: ARDUINO.27; also elsewhere on the board
SPAREIO_3: ARDUINO.29; also elsewhere on the board
SPAREIO_4: ARDUINO.31; also elsewhere on the board
SPAREIO_5: ARDUINO.33; also elsewhere on the board
SPAREIO_6: ARDUINO.35; also elsewhere on the board
SPAREIO_7: ARDUINO.37; also elsewhere on the board
SPAREIO_8: ARDUINO.39; also elsewhere on the board
SPAREIO_9: ARDUINO.41; also elsewhere on the board
SPAREIO_10: ARDUINO.43; also elsewhere on the board
SPAREIO_11: ARDUINO.45; also elsewhere on the board
SPAREIO_12: ARDUINO.47; also elsewhere on the board
SPAREIO_13: ARDUINO.49; also elsewhere on the board
SPAREIO_14: ARDUINO.51; also elsewhere on the board
SPAREIO_15: ARDUINO.53; also elsewhere on the board
TCK: ARDUINO.A4; also elsewhere on the board
TDI: ARDUINO.A7; also elsewhere on the board
TDO: ARDUINO.A6; also elsewhere on the board
TMS: ARDUINO.A5; also elsewhere on the board
TOOL1_AIN: J11.13, J28.1, R12.2
TOOL1_AIN_BUF: ARDUINO.A12, J28.2, R12.1
TOOL1_DOUT: IC2.9 (Y1), J11.14, R33.2
TOOL1_DOUT_BUF: ARDUINO.42, IC2.11 (A1)
TOOL2_AIN: J12.13, J24.1, R13.2
TOOL2_AIN_BUF: ARDUINO.A13, J24.2, R13.1
TOOL2_DOUT: IC2.7 (Y2), J12.14, R32.2
TOOL2_DOUT_BUF: ARDUINO.50, IC2.13 (A2)
TOOL3_AIN: J13.13, J25.1, R16.2
TOOL3_AIN_BUF: ARDUINO.A15, J25.2, R16.1
TOOL3_DOUT: IC2.5 (Y3), J13.14, R31.2
TOOL3_DOUT_BUF: ARDUINO.22, IC2.15 (A3)
TOOL4_AIN: J14.13, J26.1, R18.2
TOOL4_AIN_BUF: ARDUINO.A14, J26.2, R18.1
TOOL4_DOUT: IC2.3 (Y4), J14.14, R30.2
TOOL4_DOUT_BUF: ARDUINO.26, IC2.17 (A4)
TOOL_DIR: ARDUINO.32, J11.11, J12.11, J13.11, J14.11
TOOL_SCL: J11.10, J12.10, J13.10, J14.10; also elsewhere on the board
TOOL_SDA: J11.9, J12.9, J13.9, J14.9; also elsewhere on the board
TOOL_STEP: ARDUINO.30, J11.12, J12.12, J13.12, J14.12
TX1: ARDUINO.18 (18(TX1)); also elsewhere on the board
TX2: ARDUINO.16 (16(TX2)); also elsewhere on the board
TX3: ARDUINO.14 (14(TX3)); also elsewhere on the board
VSENSE: ARDUINO.A1 (A1(TX0)); also elsewhere on the board
X1A: J4.2, J4A.2, STEPSTICK1.1A
X1B: J4.1, J4A.1, STEPSTICK1.1B
X2A: J4.3, J4A.3, STEPSTICK1.2A
X2B: J4.4, J4A.4, STEPSTICK1.2B
X_DIR: ARDUINO.36, STEPSTICK1.DIR
X_MIN_PIN: ARDUINO.A9; also elsewhere on the board
X_MS1: J18.1, R1.2, STEPSTICK1.MS1
X_MS2: J18.3, STEPSTICK1.MS2
X_MS3: J18.5, STEPSTICK1.MS3
X_STEP: ARDUINO.38, STEPSTICK1.STEP
Y1A: J5.2, J5A.2, STEPSTICK2.1A
Y1B: J5.1, J5A.1, STEPSTICK2.1B
Y2A: J5.3, J5A.3, STEPSTICK2.2A
Y2B: J5.4, J5A.4, STEPSTICK2.2B
Y_DIR: ARDUINO.A3, STEPSTICK2.DIR
Y_MIN_PIN: ARDUINO.A10; also elsewhere on the board
Y_MS1: J19.1, R6.2, STEPSTICK2.MS1
Y_MS2: J19.3, STEPSTICK2.MS2
Y_MS3: J19.5, STEPSTICK2.MS3
Y_STEP: ARDUINO.A2, STEPSTICK2.STEP
Z1A: J6.2, J6A.2, STEPSTICK3.1A
Z1B: J6.1, J6A.1, STEPSTICK3.1B
Z2A: J6.3, J6A.3, STEPSTICK3.2A
Z2B: J6.4, J6A.4, STEPSTICK3.2B
Z_DIR: ARDUINO.8, STEPSTICK3.DIR
Z_MIN_PIN: ARDUINO.A11; also elsewhere on the board
Z_MS1: J20.1, R7.2, STEPSTICK3.MS1
Z_MS2: J20.3, STEPSTICK3.MS2
Z_MS3: J20.5, STEPSTICK3.MS3
Z_STEP: ARDUINO.9, STEPSTICK3.STEP

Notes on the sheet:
I2C ADDRESS MAP: A1 A0 00: TOOL#3 01: TOOL#2 10: TOOL#1 11: TOOL#4
MODULAR TOOL #4
MODULAR TOOL #3
MODULAR TOOL #2
MODULAR TOOL #1
Drawn by: NEIL JANSEN
Checked by:
Revision B
EMC02 Motion Controller for FirePick Delta
ARDUINO MEGA 2560 OR DUE
X AXIS STEPPER DRIVER
N/C
Y AXIS STEPPER DRIVER
Z AXIS STEPPER DRIVER
Released under the Creative Commons Attribution Share-Alike 4.0 License
D54
D55
D56
D57
D58
D59
D60
D61
D62
D63
D64
D65
D66
D67
D68
D69
NOTE: DO NOT WIRE +5V FROM ARDUINO TO +5V RAIL.
MODULAR TOOL SYSTEM
DOUT 3.3V->5V BUFFERING
EMERGENCY STOP SWITCH (NORMALLY CLOSED TYPE) USE JUMPER IF NOT PRESENT
E-STOP
!EN! BUFFERING
NOTE: ACTIVE HIGH
NOTE: ACTIVE LOW
NOTE: SERVO/NEOPIXELS AREN'T ON E-STOP, THEY ARE BUFFERED TO SHIFT MCU 3.3V -> 5V


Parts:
C1, C2, C4, C5, C6, C7: 0.1u; 0805; PARTNO CC0805ZRY5V9BB104
C3: 100uF; PANASONIC_D; PARTNO 25TXV100M6.3X8
FAN1, FAN2: 22232031; MOLEX-1X3_LOCK; PARTNO 22232031
IC1, IC2: 74ACT244DW; SO20W; PARTNO 74ACT244SCX
IC3: INA168; SOT23-5; PARTNO INA168NA/3K
J1, J2, J3, J17, J27, J29, J30: CONN-0.1-S-1X3; MA03-1; PARTNO CONN-0.1-S-1X3
J7, J8, J9: CONN-0.1-RA-1X3; MA03-1; PARTNO CONN-0.1-RA-1X3
J7A, J8A, J9A: CONN-RECT-3PINJST_PH_2MM; CONN-JST_PH-2.0MM-3PIN-SMT-RA
J10: MA05-2
J15: DNP; MA04-1
J16: CONN-0.1-S-1x18; MA18-1
J21: MA09-1
J22: OSTOP050000; CONN-OSTOP050000; PARTNO OSTOP240000
J22A: OSTTH050160; CONN-OSTTH050160; PARTNO OSTTH050160
J23: ICSP/SPI; MA03-2
LED1, LED2, LED3: AMBER; LED-1206-NO_SILK; PARTNO LTST-C150AKT
LOGO1: LOGO-FIREPICKLARGE; LOGO-FIREPICK
LOGO2: LOGO-OSHWMEDIUM; LOGO-OSHW-MEDIUM
LOGO3: LOGO-CC-BY-SALARGE; LOGO-CC-BY-SA
Q1, Q2, Q3, Q4: BSS138; SOT23; PARTNO BSS138
R3, R4, R5: 1k; 0805; PARTNO RC0805FR-071KL
R10, R11, R14, R15: 4.7K; 0805; PARTNO RC0805FR-074K7L
R17, R20, R21: 20K; 0805; PARTNO RC0805FR-0720KL
R25, R26, R27, R36, R46, R47: 10K; 0805; PARTNO RC0805FR-0710KL
R34: 1.0 mOhm; CHIP-1224-KELVIN; PARTNO LVK25R001FER
R35: 4.7K 0.1%; 0805; PARTNO *
R37: 4.7k 0.1%; 0805; PARTNO *
R38, R39: DNP; 0805
R44: 100K; 0805; PARTNO *
R45: 10k 0.1%; 0805; PARTNO *
S1: TAC_SWITCHSMD; TACTILE_SWITCH_SMD; PARTNO SWITCH TACTILE SPST-NO 0.05A 12V
TP2: +12V; CON-TESTPOINT
TP3: GND; CON-TESTPOINT
TP4: +5V; CON-TESTPOINT
TP5: +3.3V; CON-TESTPOINT

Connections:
3.3V: TP5.1; also elsewhere on the board
12V: FAN1.2, FAN2.2, R34.V2, TP2.1; also elsewhere on the board
20_SDA: J21.3; also elsewhere on the board
21_SCL: J21.2; also elsewhere on the board
!PS_ON: J22.4, Q3.3 (D)
!PS_ON_BUF: Q3.1 (G), R36.2; also elsewhere on the board
!RESET: J10.6, J23.2, S1.3, S1.4; also elsewhere on the board
!TRST: J10.8
+5V: C1.1, C2.1, C3.+, C4.1, IC1.20 (VCC), IC2.20 (VCC), J1.2, J2.2, J3.2, J7.2, J7A.2, J8.2, J8A.2, J9.2, J9A.2, J15.1, J16.1, J17.2, J22.5, J23.5, R3.2, R4.1, R5.1, R14.2, R15.2, TP4.1; also elsewhere on the board
+5V_STANDBY: J22.2
AVR_RXD: LED3.C; also elsewhere on the board
AVR_TXD: LED2.C; also elsewhere on the board
D13_LED: LED1.C; also elsewhere on the board
FAN2_PWM: Q4.1 (G), R46.2; also elsewhere on the board
FAN2_TACH: FAN2.3, R47.2; also elsewhere on the board
GND: C1.2, C2.2, C3.-, C4.2, C5.2, C6.2, C7.2, FAN1.1, IC1.10 (GND), IC2.10 (GND), IC3.2 (V-), J1.3, J2.3, J3.3, J7.3, J7A.3, J8.3, J8A.3, J9.3, J9A.3, J10.2, J10.10, J15.2, J16.18, J17.3, J21.1, J22.3, J23.1, Q3.2 (S), Q4.2 (S), R17.1, R20.1, R21.1, R36.1, R37.1, R44.1, S1.1, S1.2, TP3.1; also elsewhere on the board
IOREF: J10.4, Q1.1 (G), Q2.1 (G), R10.2, R11.2, R46.1, R47.1; also elsewhere on the board
ISENSE: C6.1, IC3.1 (OUT), R44.2; also elsewhere on the board
MISO: J23.6; also elsewhere on the board
MOSI: J23.3; also elsewhere on the board
unnamed: R35.1, R45.2
unnamed: FAN2.1, Q4.3 (D)
unnamed: J22.1, R34.V1
unnamed: LED1.A, R3.1
unnamed: J27.3, R17.2
unnamed: J29.3, R20.2
unnamed: J30.3, R21.2
unnamed: C7.1, IC3.3 (IN+), IC3.5 (V+), R34.I1, R35.2
unnamed: IC3.4 (IN-), R34.I2
unnamed: LED2.A, R4.2
unnamed: LED3.A, R5.2
RX1: J21.4; also elsewhere on the board
RX2: J21.6; also elsewhere on the board
RX3: J21.8; also elsewhere on the board
SCL: Q2.2 (S), R10.1, R38.1; also elsewhere on the board
SCLK: J23.4; also elsewhere on the board
SDA: Q1.2 (S), R11.1, R39.1; also elsewhere on the board
SERVO1: J1.1; also elsewhere on the board
SERVO2: J2.1; also elsewhere on the board
SERVO3: J3.1; also elsewhere on the board
SERVO4: J17.1; also elsewhere on the board
SPAREIO_0: J16.2; also elsewhere on the board
SPAREIO_1: J16.3; also elsewhere on the board
SPAREIO_2: J16.4; also elsewhere on the board
SPAREIO_3: J16.5; also elsewhere on the board
SPAREIO_4: J16.6; also elsewhere on the board
SPAREIO_5: J16.7; also elsewhere on the board
SPAREIO_6: J16.8; also elsewhere on the board
SPAREIO_7: J16.9; also elsewhere on the board
SPAREIO_8: J16.10; also elsewhere on the board
SPAREIO_9: J16.11; also elsewhere on the board
SPAREIO_10: J16.12; also elsewhere on the board
SPAREIO_11: J16.13; also elsewhere on the board
SPAREIO_12: J16.14; also elsewhere on the board
SPAREIO_13: J16.15; also elsewhere on the board
SPAREIO_14: J16.16; also elsewhere on the board
SPAREIO_15: J16.17; also elsewhere on the board
TCK: J10.1; also elsewhere on the board
TDI: J10.9; also elsewhere on the board
TDO: J10.3; also elsewhere on the board
TMS: J10.5; also elsewhere on the board
TOOL_SCL: J15.3, Q2.3 (D), R15.1, R38.2; also elsewhere on the board
TOOL_SDA: J15.4, Q1.3 (D), R14.1, R39.2; also elsewhere on the board
TX1: J21.5; also elsewhere on the board
TX2: J21.7; also elsewhere on the board
TX3: J21.9; also elsewhere on the board
VSENSE: C5.1, R37.2, R45.1; also elsewhere on the board
X_MIN_PIN: J30.2, R25.1; also elsewhere on the board
X_STOP: J7.1, J7A.1, J30.1, R25.2
Y_MIN_PIN: J29.2, R26.1; also elsewhere on the board
Y_STOP: J8.1, J8A.1, J29.1, R26.2
Z_MIN_PIN: J27.2, R27.1; also elsewhere on the board
Z_STOP: J9.1, J9A.1, J27.1, R27.2

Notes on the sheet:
Drawn by: NEIL JANSEN
Checked by:
Revision B
EMC02 Motion Controller for FirePick Delta
Released under the Creative Commons Attribution Share-Alike 4.0 License
**TODO:
* Replace StepSticks with DRV8825's
* Add digital potentiometer adjustment circuit for DRV8825's
* Replace BSS138's on I2C bus with PCA9512? (hot swap protection)
SPI BUS
I2C
TEST POINTS
AVR JTAG
WARNING: +5V SUPPLY *MUST* BE ABLE TO SUPPLY AT LEAST 60 mA PER NEOPIXEL!
+12V FANS
SPARE I/O
SERVOS OR NEOPIXELS
RESET BUTTON
STATUS LEDS
ENDSTOP 5V->3.3V
ENDSTOPS
I2C 5V<->3.3V
LOGIC IC PWR
POWER
Revision --: First dev release
Revision A: Arduino Due support added
NOTE: DECOUPLE W/CAPACITORS AT NEOPIXEL END SEE ADAFRUIT UBERGUIDE FOR MORE INFO: https://learn.adafruit.com/adafruit-neopixel-uberguide/overview
* NOTE: THIS IS A 2-PIECE TERMINAL STRIP. - THE OSTOP IS THE MALE PIN HEADER - THE OSTTH IS THE PLUG-ON SCREW TERMINAL
Isense Vout=(Is)(Rs)(200uA/V)(RL) = 15A * 0.001 ohm * 0.0002 A/V * RL
Revision B: Added R36,R45,C7. Unconnected Arduino VIN to +12V. Fixed PCB routing issue. Moved TOOL4_DOUT_BUF and !TOOL4_EN_BUF! from 18/19 to
TODO: INSTALL FERRITE BEAD ON ISENSE?
SERIAL
NOTE: FAN1 IS INTENDED FOR END EFFECTOR (CONSTANT ON) FAN2 IS INTENDED FOR PLA COOLING (SWITCHED)

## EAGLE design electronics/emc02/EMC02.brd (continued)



Board: 2 copper layers, 150.0 x 129.9 mm, 135 parts (4 on the bottom side), 144 nets.

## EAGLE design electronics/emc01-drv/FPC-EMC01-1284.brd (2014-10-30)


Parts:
C1, C5, C7, C8: 0.1 uF; 0805
C2: 1uF; 0805
C3, C11: 22P; 0805
C4, C9: 0.1uF; 0805
F1: 500mA; PTC-1206
J1: USB-MINIB-5PIN; USB-MINIB
J2: CONN-MOLEX-MICROFIT-6PIN; CONN-MOLEX-MINIFIT-6PIN-2ROW
J3: DNP; MA06-1
J4: MA04-1
J4A: MOT-X; CONN-JST-PH_2.0MM_4PIN-SMT-RA
J7, J8, J9: MA03-1
J7A, J8A, J9A: CONN-RECT-3PINJST_PH_2MM; CONN-JST_PH-2.0MM-3PIN-SMT-RA
J11, J12, J13, J14: CONN-RECT-16PIN-2ROW; CONN-RECT-2.54MM-16PIN-2ROW-SMTH
J15: DNP; MA04-1
J16: ICSP; CONN-RECT-2.54MM-6-PIN-2ROW-SMTH
LED1: Green; LED-1206-NO_SILK
LED2: Red; LED-1206-NO_SILK
LED3: Yellow; LED-1206-NO_SILK
LOGO4: LOGO-FIREPICKLARGE; LOGO-FIREPICK
LOGO5: LOGO-OSHWMEDIUM; LOGO-OSHW-MEDIUM
LOGO6: LOGO-CC-BY-SALARGE; LOGO-CC-BY-SA
R1, R2: 10K; 0805
R3, R4, R5, R6, R7: 1k; 0805
R8, R9: 22; 0805
R12, R13: 4.7K; 0805
S1: TAC_SWITCHSMD; TACTILE_SWITCH_SMD
TP1: PD2; CON-TESTPOINT
TP2: +12V; CON-TESTPOINT
TP3: GND; CON-TESTPOINT
TP4: +5V; CON-TESTPOINT
TP5: +3.3V; CON-TESTPOINT
U1: AT90USB1287-AU; QFP80P1600X1600X120-64N
U2: PRTR5V0U4D; SOT23-6
X1: 20MHz; CTS406

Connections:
3.3V: TP5.1
12V: J2.1, J2.2, J2.3, J11.5, J11.6, J11.7, J11.8, J12.5, J12.6, J12.7, J12.8, J13.5, J13.6, J13.7, J13.8, J14.5, J14.6, J14.7, J14.8, TP2.1
!RESET: C9.2, J16.2, R1.1, S1.3, S1.4, U1.20 (~RESET)
!XYZ_ENABLE: R2.1, U1.35 (PC0)
+5V: C1.1, C5.1, C7.1, C8.1, F1.2, J3.4, J7.2, J7A.2, J8.2, J8A.2, J9.2, J9A.2, J15.1, J16.5, R1.2, R2.2, R3.2, R4.1, R5.1, R12.2, R13.2, TP4.1, U1.3 (UVCC), U1.21 (VCC_2), U1.52 (VCC), U1.64 (AVCC)
AREF: C4.1, U1.62 (AREF)
AVR_RXD: J3.3, R6.1, U1.27 (PD2)
AVR_TXD: J3.2, R7.1, U1.28 (PD3)
D+: R9.2, U1.5 (D+), U2.1 (IO1)
D-: R8.2, U1.4 (D-), U2.3 (IO2)
DTR: C9.1, J3.1
GND: C1.2, C2.1, C3.2, C4.2, C5.2, C7.2, C8.2, C11.2, J1.GND, J1.MTN1 (MTN2), J1.MTN2 (MTN3), J1.MTN3 (MTN1), J1.MTN4, J2.4, J2.5, J2.6, J3.5, J3.6, J7.3, J7A.3, J8.3, J8A.3, J9.3, J9A.3, J11.1, J11.2, J11.3, J11.16, J12.1, J12.2, J12.3, J12.4, J13.1, J13.2, J13.3, J13.4, J13.16, J14.1, J14.2, J14.3, J15.2, J16.1, LED1.C, S1.1, S1.2, TP3.1, U1.6 (UGND), U1.22 (GND_2), U1.53 (GND_3), U1.63 (GND), U2.2 (GND)
MISO: J16.6, U1.13 (PB3)
MOSI: J16.3, U1.12 (PB2)
unnamed: J1.D-, R8.1
unnamed: J1.D+, R9.1
unnamed: LED1.A, R3.1
unnamed: LED2.A, R4.2
unnamed: LED3.A, R5.2
RXD: R7.2
RXLED: LED3.C
SCL: J11.10, J12.10, J13.10, J14.10, J15.3, R12.1, U1.25 (PD0)
SCLK: J16.4, U1.11 (PB1)
SDA: J11.9, J12.9, J13.9, J14.9, J15.4, R13.1, U1.26 (PD1)
SDCS: U1.10 (PB0)
SPARE: TP1.1, U1.43 (PE2)
TOOL1_AIN: J11.13, U1.61 (PF0)
TOOL1_DOUT: J11.14, U1.60 (PF1)
TOOL1_ENABLE: J11.15, U1.17 (PB7)
TOOL2_AIN: J12.13, U1.59 (PF2)
TOOL2_DOUT: J12.14, U1.58 (PF3)
TOOL2_ENABLE: J12.15, U1.16 (PB6)
TOOL3_AIN: J13.13, U1.56 (PF5)
TOOL3_DOUT: J13.14, U1.57 (PF4)
TOOL3_ENABLE: J13.15, U1.15 (PB5)
TOOL4_AIN: J14.13, U1.54 (PF7)
TOOL4_DOUT: J14.14, U1.55 (PF6)
TOOL4_ENABLE: J14.15, U1.14 (PB4)
TOOL_DIR: J11.11, J12.11, J13.11, J14.11, U1.44 (PA7)
TOOL_STEP: J11.12, J12.12, J13.12, J14.12, U1.45 (PA6)
TXD: R6.2
TXLED: LED2.C
UCAP: C2.2, U1.7 (UCAP)
VBUS: U1.8 (VBUS), U2.5 (VCC)
VUSB: F1.1, J1.VBUS
X1A: J4.2, J4A.2
X1B: J4.1, J4A.1
X2A: J4.3, J4A.3
X2B: J4.4, J4A.4
XTAL1: C3.1, U1.24 (XTAL1), X1.3 (2)
XTAL2: C11.1, U1.23 (XTAL2), X1.1
X_DIR: U1.50 (PA1)
X_STEP: U1.51 (PA0)
X_STOP: J7.1, J7A.1, U1.9 (PE3)
Y_DIR: U1.48 (PA3)
Y_STEP: U1.49 (PA2)
Y_STOP: J8.1, J8A.1, U1.18 (PE4)
Z_DIR: U1.46 (PA5)
Z_STEP: U1.47 (PA4)
Z_STOP: J9.1, J9A.1, U1.19 (PE5)

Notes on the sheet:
I2C ADDRESS MAP: A1 A0 00: TOOL#3 01: TOOL#2 10: TOOL#1 11: TOOL#4
MODULAR TOOL #4
MODULAR TOOL #3
MODULAR TOOL #2
MODULAR TOOL #1
5V (FTDI Passthru header, provision for FTDI driver but do not populate for cost reduction)
Drawn by: NEIL JANSEN, DAYTON PIDHIRNEY
Checked by:
v0.1
EMC01 Motion Controller for FirePick Delta
ATMEL AT90USB1287-AU
USB-TO-TTL SERIAL
X AXIS STEPPER DRIVER
ENDSTOPS
MODULAR TOOL SYSTEM
FTDI SERIAL HEADER
+12VDC IN
ICSP
I2C
TEST POINTS
N/C
Released under the Creative Commons Attribution Share-Alike 4.0 License
ESD
LEDS


Board: 2 copper layers, 100.0 x 86.6 mm, 53 parts (0 on the bottom side), 48 nets.

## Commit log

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2014-06-13 updating PCB and adding GERBERS+BOM
    [BOM.xls, OPTO.brd]
2014-06-13 Fixed silkscreen and updated gerbers to final rev
    [OPTO.brd]
2014-06-16 Rev. A for RS485 to Servo and Accelerometer
    [FPRX.kicad_pcb, FPRX.sch]
2014-06-17 Rev. A PCB HDMI to FPC converter, for RPi Cam
    [FireExtender.kicad_pcb, FireExtender.sch]
2014-06-17 Removed unused components from schematic, added WS2812 LED, changed C18 to C17
    [FPRX.kicad_pcb, FPRX.sch]
2014-06-17 Added components reference to silkscreen
    [FireExtender.kicad_pcb]
2014-06-17 Added title to worksheet for SCH, added image of PCB and PDF of schematic
    [FireExtender.sch]
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2014-06-17 Added reference for C11 & C12
    [FPRX.kicad_pcb]
2014-06-18 Added resistor for WS2812 onboard LED, connected to the right input
    [FPRX.kicad_pcb, FPRX.sch]
2014-06-18 Differential traces are length matched now
    [FireExtender.kicad_pcb]
2014-06-23 New chip and layout + A axis motor controller/Board still not finalized
    [FPC EMC01 1284.brd, FPD EMC01.brd]
2014-06-23 adding new unfinished PCB
    [LCD board.brd, LCD board.sch]
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2014-06-24 added new unfinished PCB
    [HotStick.brd, HotStick.sch]
2014-06-24 Added modular tool connectors, RasPi connector, Front Panel connector.
    [FPC EMC01 1284.brd]
2014-06-24 Fixed File
    [HotStick.brd]
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2014-06-24 Revert "recover lost changes"
    This reverts commit 0ce016bf4596014ad1f4ff05d6638003136b1386.
    [FPC EMC01 1284.brd]
2014-06-24 Restore Neil's changes 1d1a
    [FPC EMC01 1284.brd]
2014-06-24 adding Dayton's 5958 ICSP/Power circuits to Neil's board
    [FPC EMC01 1284.brd]
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2014-06-24 Fixed schematics
    looks more uniform
    [FPC-EMC01-1284.brd]
2014-06-24 Added FFC connector from HDMI
    [FPC-EMC01-1284.brd]
2014-06-24 Fixed errors/connectors
    Fixed the ERC errors, ones that are left just ignore. Neil needs to add
    his library of proper JST connectors to the board and we will be pretty
    much ready to route.
    [FPC-EMC01-1284.brd]
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2014-06-26 Added pcb outline for FPC-EMC01-1284.brd, and placed connectors per AutoCAD DXF. Added male 16-pin connector to firepick.lbr.
    [FPC-EMC01-1284.brd]
2014-06-26 Moved stepper driver IC's to symmetrically-pleasing locations
    [FPC-EMC01-1284.brd]
2014-06-26 minor tweaks before layout
    [FPC-EMC01-1284.brd]
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2014-06-27 Mashed everything on the board
    Still trying to figure out optimal positioning for all the SMT parts.
    New 5V Reg to be placed on next commit.
    [FPC-EMC01-1284.brd]
2014-07-04 Changed connector on LCD board. Added notes to EMC01 board.
    [FPC-EMC01-1284.brd, LCD board.brd, LCD board.sch]
2014-07-06 Wired up encoder, switches, and LEDs
    [LCD board.brd, LCD board.sch]
2014-07-07 Redesigned with Micro USB instead of Microfit. PCB is now smaller. Using I2C to communicate with motion controller
    [FPRX.kicad_pcb, FPRX.sch]
2014-07-11 adding bom markdown generation scripts, testing FireBOM URL /github path
    [BOM.csv]
2014-07-11 moving BOM to firepick-delta.wiki
    [BOM.csv]
2014-07-11 KiCAD version of the opto-endstop. Adding transistor for LED
    [eopto01.kicad_pcb, eopto01.sch]
2014-07-11 Forgot how to Eagle, but added DC/DC. Change components for better specs
    [FPC-EMC01-1284.brd]
2014-07-12 Added JST connector for Opto-endstop
    [eopto01.kicad_pcb, eopto01.sch]
2014-07-14 Added StepStick to library, and updated EMC01 schematic/pcb
    [FPC-EMC01-1284.brd]
2014-07-15 fixing I2C connectors, adding FTDI, adding sch for motor controllers
    [FPC-EMC01-1284.brd]
2014-07-15 Changed to Sparkfun Micro USB connector
    [FPRX.kicad_pcb, FPRX.sch]
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2014-07-31 added jigs/fixtures, adding component feeder mount assembly
    [J0002 - Carbon rod saw jig - Front mount.stl, J0003 - Carbon rod saw jig - Rear mount.stl, J0004 - Carbon rod saw jig - L-bracket.stl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]
2014-08-01 Adding 2D prints and DXF's for acrylic frame plates
    [PC01 - Top plate.dxf, PC02 - Bottom plate.dxf, PC03 - Delta motor plate.dxf]
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2014-08-01 Fixing issue where Cubify was bitching about problems encountered while loading AD0001 - Frame.AD_ASM
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2014-08-02 Adding stuff for SMT nozzle, and checking in some stuff that I somehow missed
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2014-08-12 Adding new PCB assembly for Raspberry Pi B+ HAT.
    [ERPIHAT01.brd, ERPIHAT01.sch]
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2014-08-13 - Swapped FT232RL for FT231XS (copied/pasted to Sparkfun RedBoard) - Replaced micro USB with mini USB - Deleted second micro USB and Z probe pin (we can use a modular connector Z probe instead rather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
    [FPC-EMC01-1284.brd]
2014-08-14 Fixed 608 bearing block nut trap clearance Fixed bottom plate, added clearance slots for Misumi diagonal braces, which have alignment tabs.
2014-08-14 Updated 608 bearing block STL and bottom plate DXF after making fixes from last commit
    [3D0001 - Delta motor Assembly - 608 bearing block.stl, PC02 - Bottom plate.dxf]
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2014-08-28 Changed to correct pinout for Type A HDMI
    [FireExtender.kicad_pcb, FireExtender.sch]
2014-08-28 PushPlastics orange 3mm PLA @ 220C/60-50C TAZ4. 2.5hrs
    [3D0456 - Delta motor assembly - Stepper mount (plated-wide).stl]
2014-08-30 Loose Fit for delta drive parts
    [3D0001-L - Delta motor Assembly - 608 bearing block.stl, 3D0002-L - Delta motor assembly - Pulley (150T).stl, 3D0003-L - Delta motor assembly - Delta arm 90mm 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]
2014-09-02 Cleaned up EMC01 board and finalized for peer review
    [FPC-EMC01-1284.brd]
2014-09-03 Cleaned up ERPIHAT01 board and finalized for peer review
    [ERPIHAT01.brd, ERPIHAT01.sch]
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2014-09-04 Fixed minor issues and changed modular tool connector pinout to allow better routing of GND and +12V planes
    [FPC-EMC01-1284.brd, FPC-EMC01-1284.sch]
2014-09-07 Updated all EAGLE PCB's for first Prototype production run.
    [EAT0001.GBL, EAT0001.GBO, EAT0001.GBP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]
2014-09-09 REVISION A of EMC01 board. Fixed unconnected wires on TOOL1_ENABLE, TOOL2_ENABLE, TOOL3_ENABLE, and TOOL4_ENABLE. This was discovered by Seeed Studio Fusion PCB service after being submitted to be ma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
    [FPC-EMC01-1284.brd, FPC-EMC01-1284.sch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]
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2014-09-12 Mirror plate. A calibration hunch. Let's see where it goes...
    [J0014 - mirror plate.skp]
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2014-09-24 Merged in STL fix for 3D0051 from dev-loose
    [3D0051 - Extrusion corner bracket.stl, 3D0051.stl]
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2014-10-02 Revision A, after assembling first batch of PCBs.
    [EAT0001.brd, EAT0001.sch, EHDMIFPC01.sch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]
2014-10-08 * New Ball-stud delta rods * Updates for new PCB assemblies * Updates for LCD bezel assembly * Updates for modular tools * Other misc stuff
    [3D0003 - Delta motor assembly - Delta arm 90mm (Traxxas 5347).stl, 3D0013 - Bracket - Power outlet - IEC.stl, 3D0015 - EMC01 mounting plate.stl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]
2014-10-08 Adding LCD bezel, fixing corner brackets
    [3D0004 - Delta motor assembly - Stepper bracket.stl, 3D0005 - Delta motor assembly - Stepper bracket mating side.stl, 3D0006 - Delta motor assembly - Limit swi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]
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2014-10-22 Continuing work on feeders, cameras, and other misc mechanical pieces
    [3D0010 - Extrusion nut (M5).stl, 3D0026a - Up-looking camera housing - Leopard LI-OV5640-USB-72.stl, 3D0027a - Up-looking camera housing base - Leopard LI-OV56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]
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2014-10-29 New MCU Conversion
    AT90 is hooked up in schematic
    [FPC-EMC01-1284.brd, FPC-EMC01-1284.sch]
2014-10-30 EMC01 Revision B: Added +5V voltage regulator and other misc stuff
    [FPC-EMC01-1284.GBL, FPC-EMC01-1284.GBO, FPC-EMC01-1284.GBP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]
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2014-11-04 Nut trap, broken assembly
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2014-11-09 Eliminate catenary spring rattle by reducing hole size
    [3D0234 - Delta rod (full-length).stl]
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2014-11-10 Revert "Modify bearing block to accept Nyloc nuts"
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2014-11-23 Arm collision fix
    [3DLC0456 - Delta stepper mount (plated).stl, 3DLC0456 Delta stepper mount (plated).stl, 3DLC0456 Delta stepper mount.stl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]
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2015-04-11 added brim and fixed bridging issue
    [3D0053 - External ATX supply coverplate.stl]
2015-05-06 Removing STL's from mechanical (moving them to 'production files' dir)
    [3D0001a - Delta motor Assembly - 608 bearing block.stl, 3D0002b - Delta motor assembly - Pulley (150T).stl, 3D0003a - Delta motor assembly - Delta arm 90mm.stl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]
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2015-05-08 Fixed frame mounting screw hole. Reverting back to M5 hardware from M3X which didn't work as expected... The M3X needs more work before it can be re-introduced.
    [3DAT0005 - Vacuum pump mount.stl]
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2015-05-14 new stuff, checking in before bay area trip
    [3D0052 - Heated Bed Bracket.stl, 3D0456ab Delta stepper mount.stl, 3D0456c Delta stepper mount.stl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]
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

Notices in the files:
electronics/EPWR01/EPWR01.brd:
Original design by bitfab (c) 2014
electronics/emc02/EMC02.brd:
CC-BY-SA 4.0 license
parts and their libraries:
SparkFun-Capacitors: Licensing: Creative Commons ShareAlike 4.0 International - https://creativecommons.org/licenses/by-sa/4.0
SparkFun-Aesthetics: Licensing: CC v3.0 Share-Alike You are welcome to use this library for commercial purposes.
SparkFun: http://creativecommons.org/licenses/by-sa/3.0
